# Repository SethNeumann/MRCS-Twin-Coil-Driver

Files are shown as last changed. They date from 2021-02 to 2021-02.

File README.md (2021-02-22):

# REPO NAME: MRCS-Twin-Coil-Driver
## License: Creative Commons Attribution-NonCommercial-ShareAlike

Twin Coil Machines present some challenges:

    They tend to slam the points into the stock rails, eventually damaging the connection to the throwbar and the spikes or solder holding the stock rails down 
    can loosen or break.  They make a lot of electrical noise when the power is removed from the coils, which gets into other electronics, causing false operation.
    The coils will overheat and become damaged, if not catch fire, if current is applied for an extended period.
    
    In the past, Capacitive Discharge (CD) supplies were used to make an affordable supply that would protect the coil by not recharging while connected and limiting
    the constant current in case the controls failed and permanently energized the coil.

Our design drives both mild (Atlas, Bachmann, Lifelike, Peco) and "Nasty" PFM, Tenshodo, Ken Kidder, NJ International Twin Coil type machines.  The Twin Coil Driver
(TCD) shapes the pulses driving the switch machines to soften both the physical and electrical blow, reducing electrical noise and physical impact.  Pulse timing is
done in hardware (no chance of a software hang leaving power on).  The TCD works with CD power supplies and modern power supplies such as those used for LEDs, or
inexpensive bench supplies.  

The Twin Coil Driver has internal spike suppression diodes.  Input is logic level and the coils are fired on the rising and falling edge, so a simple toggle switch 
or logic level input controls the machine.

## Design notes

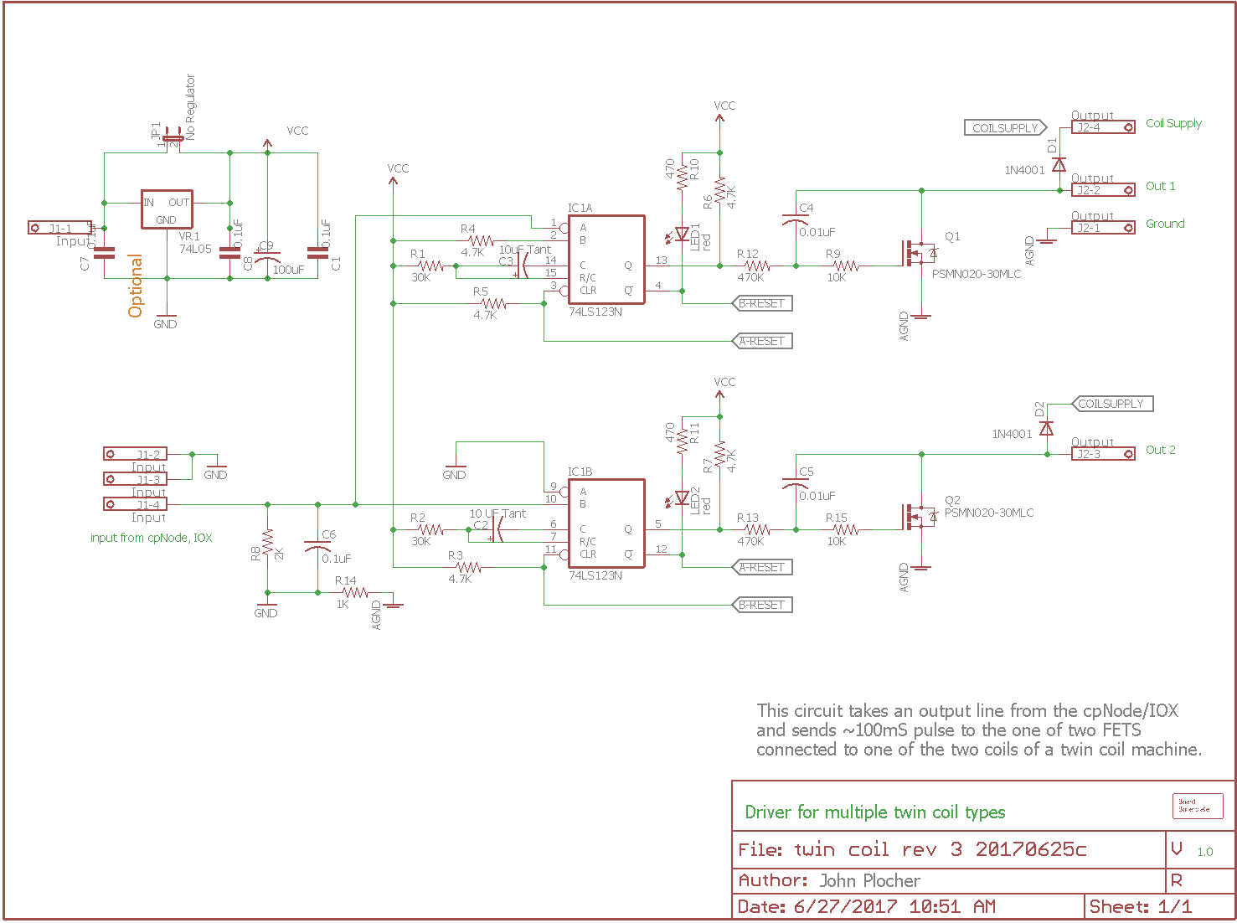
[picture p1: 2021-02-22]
MRCS-Twin-Coil-Driver-Schematic.png

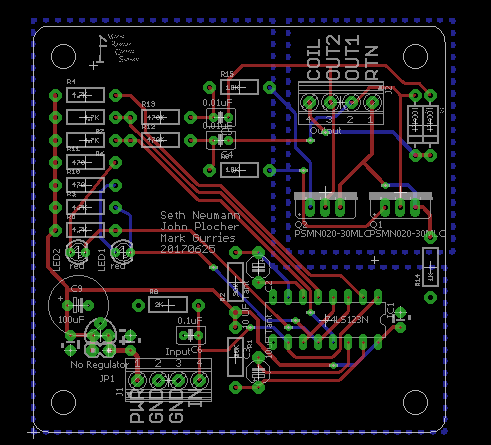
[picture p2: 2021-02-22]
MRCS-Twin-Coil-Driver-layout.png

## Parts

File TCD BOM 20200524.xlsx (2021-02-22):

Qty | Value | Device | Package | Parts | Description | MRCS | Jameco | Banggood | Leads | Leads Extd | unit | Extd | EOQ
1 |  | BOARD69X70 | BOARD-DINRAIL-2.7INX7CM | BOARD1 |  | TOB-BB |  |  |  | 0 | $1.00 | $1.00 | 5
2 | .022 uF | C-US025-030X050 | C025-030X050 | C4, C5 | CAPACITOR Monolithic .022 @ 50V 223 |  | 2306383 |  | 2 | 4 | $0.15 | $0.30 | 100
4 | 0.1uF | C-US025-030X050 | C025-030X050 | C1, C6, C7, C8 | Capacitor - Monolithic 0.1 (104) @ 50V |  | 2295911 |  | 2 | 8 | $0.02 | $0.08
2 | 10 UF Tant | CPOL-USE5-4 | E5-4 | C2, C3 | POLARIZED CAPACITOR, American symbol |  |  |  | 2 | 4 | $0.45 | $0.90 | 20
1 | 100uF | CPOL-USE3.5-10 | E3,5-10 | C9 | POLARIZED CAPACITOR, American symbol |  | 29962 |  | 2 | 2 | $0.16 | $0.16 | 10
1 | 1K | RESISTORPTH-1/4W | AXIAL-0.4 | R14 | Resistor 1K 1/4W |  | 690865 |  | 2 | 2 | $0.01 | $0.01 | 100
2 | 10K | RESISTORPTH-1/4W | AXIAL-0.4 | R9, R15 | Resistor 10K 1/4W |  | 691104 |  | 2 | 4 | $0.01 | $0.02 | 100
2 | 1N4001 | DIODEPTH | DIODE-1N4001 | D1, D2 | Diode 1N4004 |  | 35991 |  | 2 | 4 | $0.06 | $0.12 | 100
3 | 2K | RESISTORPTH-1/4W | AXIAL-0.4 | R8, 10,11 | Resistor 2K 1/4W |  | 690865 |  | 2 | 6 | $0.02 | $0.06 | 100
2 | 30K | RESISTORPTH-1/4W | AXIAL-0.4 | R1, R2 | Resistor 30K 1/4W |  | 691219 |  | 2 | 4 | $0.02 | $0.04 | 100
5 | 4.7K | RESISTORPTH-1/4W | AXIAL-0.4 | R3, R4, R5, R6, R7 | Resistor 4.7K 1/4 W |  | 691024 |  | 2 | 10 | $0.02 | $0.10 | 100
2 | 470K | RESISTORPTH-1/4W | AXIAL-0.4 | R12, R13 | Resistor, 470K 1/4W |  | 691500 |  | 2 | 4 | $0.01 | $0.02 | 100
1 | 78L05 | V_REG_78L05 | TO-92 | VR1 | Voltage Regulator |  | 51182 |  | 3 | 3 | $0.25 | $0.25 | 100
1 | 74LS123N | 74LS123N | DIL16 | IC1 | Retriggerable monostable MULTIVIBRATOR |  | 46480 |  |  | 0 | $0.79 | $0.79 | 10
2 | Input, output | 4 pos 3.5mm screw | 4 pos 3.5mm screw | J1, J2 | MKDS 1/ 4-3,5 Printklemme |  | 2124411 |  | 4 | 8 | $0.49 | $0.98 | 100
1 | socket | 16 pin DIP | 16 pin DIP | IC1-s | 16 pin DIP socket |  | 112222 |  | 16 | 16 | $0.13 | $0.13 | 100
1 | No Regulator | JUMPER-2PTH_LOCK | 1X02_LOCK | JP1 | Jumper |  |  | X | 2 | 2 | $0.02 | $0.02 | 4000
2 | PSMN020-30MLC | STP5NA50 | TO220BV | Q1, Q2 | N-CHANNEL MOS FET |  | 787798 | X | 3 | 6 | $0.59 | $1.18 | 100
1 | red | LED3MM | LED3MM | LED1 | LED Green |  |  | X | 2 | 2 | $0.01 | $0.01 | 300
1 | green | LED3MM | LED3MM | LED2 | LED Red |  |  | X | 2 | 2 | $0.01 | $0.01 | 300
 | BOM Cost |  |  |  |  |  |  |  |  | 91 |  | $6.18
 | BOM Markup | 20% |  |  |  |  |  |  |  |  |  | $1.24
 | BOM Subtotal |  |  |  |  |  |  |  |  |  |  | $7.42
 | Labor @ | $0.20 | per lead |  |  |  |  |  |  |  |  | $18.20
 | Labor Markup | 20% |  |  |  |  |  |  |  |  |  | $3.64
 | Labor Subtotal |  |  |  |  |  |  |  |  |  |  | $21.84
 | Cost Total |  |  |  |  |  |  |  |  |  |  | $29.26
 | e-Commerce | 10% |  |  |  |  |  |  |  |  |  | $2.93
 | Grand Total |  |  |  |  |  |  |  |  |  |  | $32.18
 | Sell |  |  |  |  |  |  |  |  |  |  | $32.00

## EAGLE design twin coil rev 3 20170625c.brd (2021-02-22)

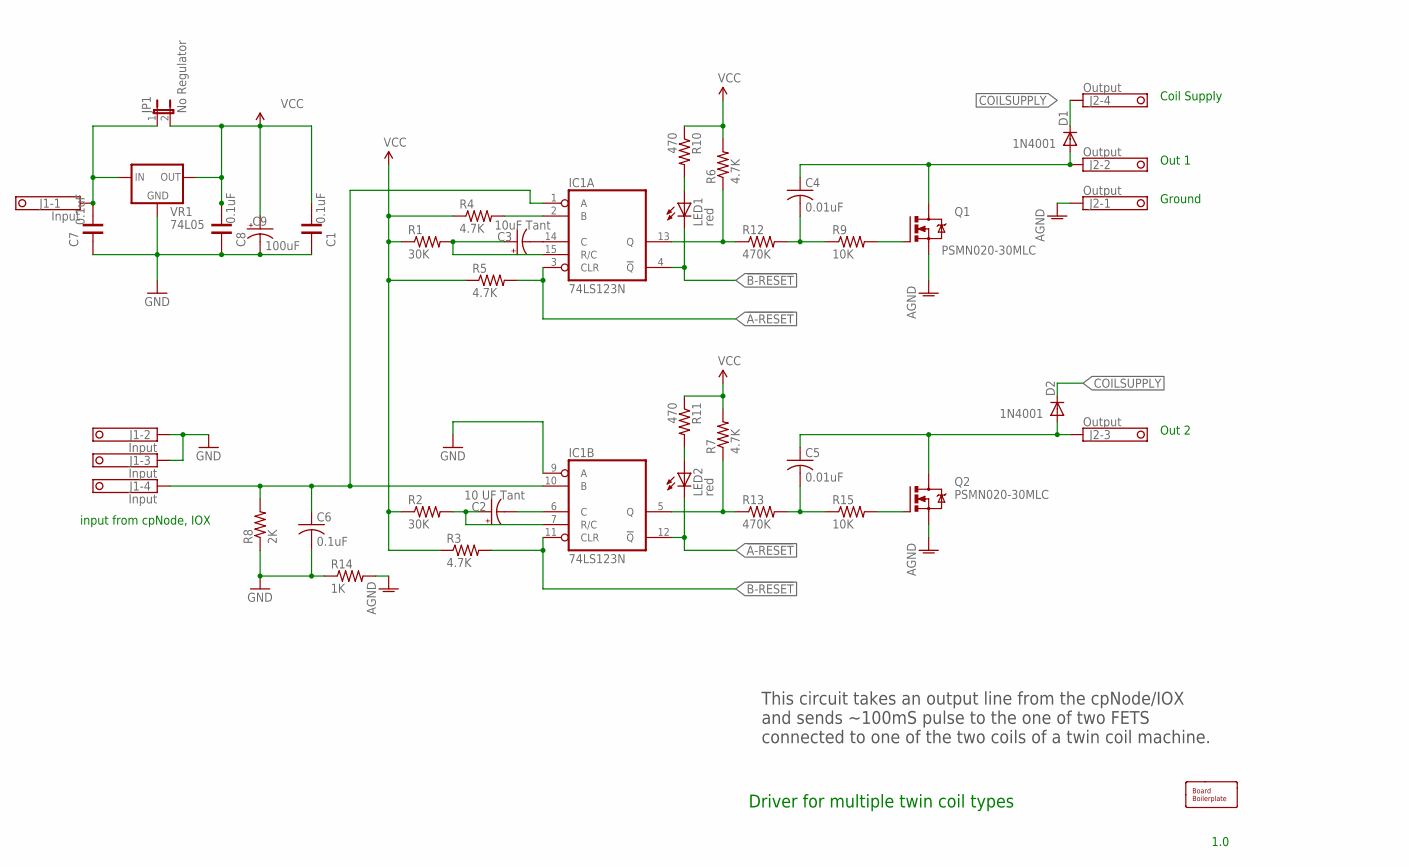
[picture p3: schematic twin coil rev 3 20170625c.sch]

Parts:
BOARD1: BOARD69X70; BOARD-DINRAIL-2.7INX7CM
C1, C7, C8: 0.1uF; CAP-PTH-SMALL
C2: 10 UF Tant; E5-4
C3: 10uF Tant; E5-4
C4, C5: 0.01uF; C025-030X050
C6: 0.1uF; C025-030X050
C9: 100uF; E3,5-10
D1, D2: 1N4001; DIODE-1N4001
IC1: 74LS123N; DIL16
J1: Input; 1751264
J2: Output; 1751264
JP1: No Regulator; 1X02_LOCK
LED1, LED2: red; LED3MM
Q1, Q2: PSMN020-30MLC; TO220BV
R1, R2: 30K; AXIAL-0.4
R3, R4, R5, R6, R7: 4.7K; AXIAL-0.4
R8: 2K; AXIAL-0.4
R9, R15: 10K; AXIAL-0.4
R10, R11: 470; AXIAL-0.4
R12, R13: 470K; AXIAL-0.4
R14: 1K; AXIAL-0.4
VR1: 74L05; TO-92

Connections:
!A-RESET: IC1.3 (CLR), IC1.12 (!Q), LED2.K (C), R5.P$2 (2)
!B-RESET: IC1.4 (!Q), IC1.11 (CLR), LED1.K (C), R3.P$2 (2)
AGND: J2.1, Q1.S, Q2.S, R14.P$2 (2)
COILSUPPLY: D1.C, D2.C, J2.4
FETDRIVE1: Q1.G, R9.P$2 (2)
GND: C1.1, C6.2, C7.1, C8.1, C9.-, IC1.8 (GND), IC1.9 (A), J1.2, J1.3, R8.P$1 (1), R14.P$1 (1), VR1.2 (GND)
INPUT: C6.1, IC1.1 (A), IC1.10 (B), J1.4, R8.P$2 (2)
unnamed: IC1.13 (Q), R6.P$1 (1), R12.P$1 (1)
unnamed: IC1.5 (Q), R7.P$1 (1), R13.P$1 (1)
unnamed: Q2.G, R15.P$2 (2)
unnamed: IC1.2 (B), R4.P$2 (2)
unnamed: C3.-, IC1.14 (C)
unnamed: C2.-, IC1.6 (C)
unnamed: C3.+, IC1.15 (R/C), R1.P$2 (2)
unnamed: C2.+, IC1.7 (R/C), R2.P$2 (2)
unnamed: C4.2, R9.P$1 (1), R12.P$2 (2)
unnamed: C5.2, R13.P$2 (2), R15.P$1 (1)
unnamed: LED1.A, R10.P$2 (2)
unnamed: LED2.A, R11.P$2 (2)
OUT1: C4.1, D1.A, J2.2, Q1.D
OUT2: C5.1, D2.A, J2.3, Q2.D
V+: C7.2, J1.1, JP1.1, VR1.3 (IN)
VCC: C1.2, C8.2, C9.+, IC1.16 (VCC), JP1.2, R1.P$1 (1), R2.P$1 (1), R3.P$1 (1), R4.P$1 (1), R5.P$1 (1), R6.P$2 (2), R7.P$2 (2), R10.P$1 (1), R11.P$1 (1), VR1.1 (OUT)

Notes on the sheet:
input from cpNode, IOX
This circuit takes an output line from the cpNode/IOX and sends ~100mS pulse to the one of two FETS connected to one of the two coils of a twin coil machine.
Coil Supply
Out 2
Out 1
Ground
Driver for multiple twin coil types
1.0

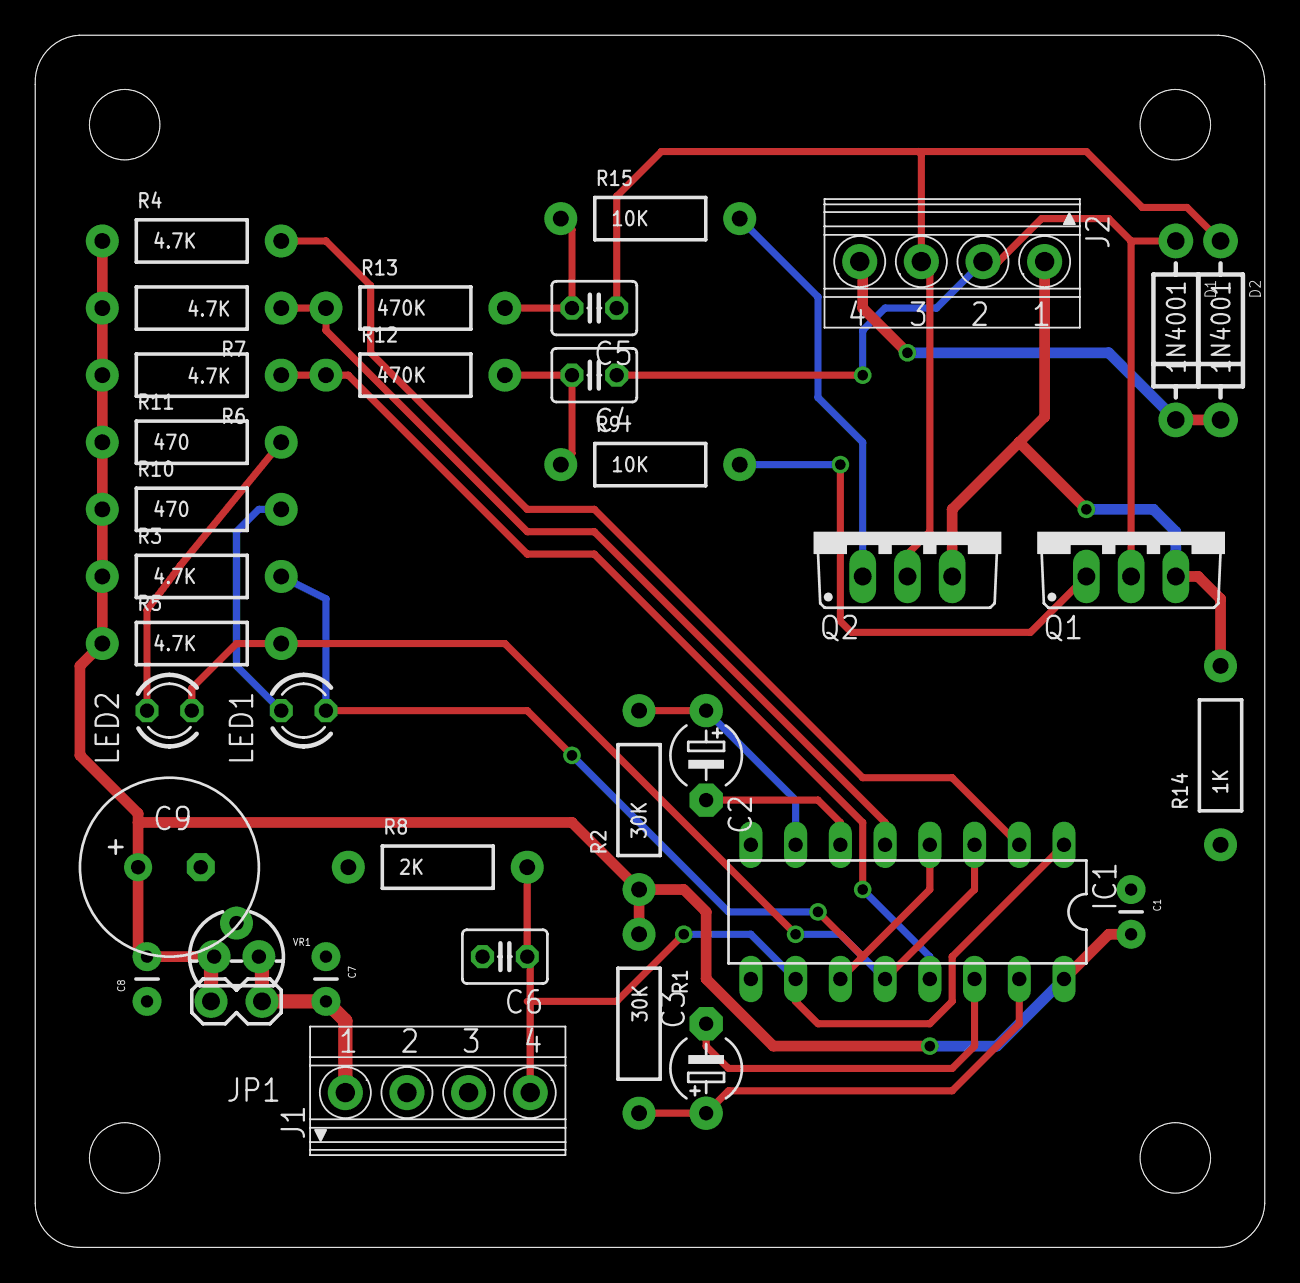
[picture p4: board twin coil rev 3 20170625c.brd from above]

Board: 2 copper layers, 69.8 x 68.8 mm, 38 parts (0 on the bottom side), 23 nets.

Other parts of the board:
U$1: CA-PROP65WARNING
U$2: MRCSLOGOTOP

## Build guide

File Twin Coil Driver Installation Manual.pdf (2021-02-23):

# Twin Coil Driver

### Revision 1.0 February 22, 2021

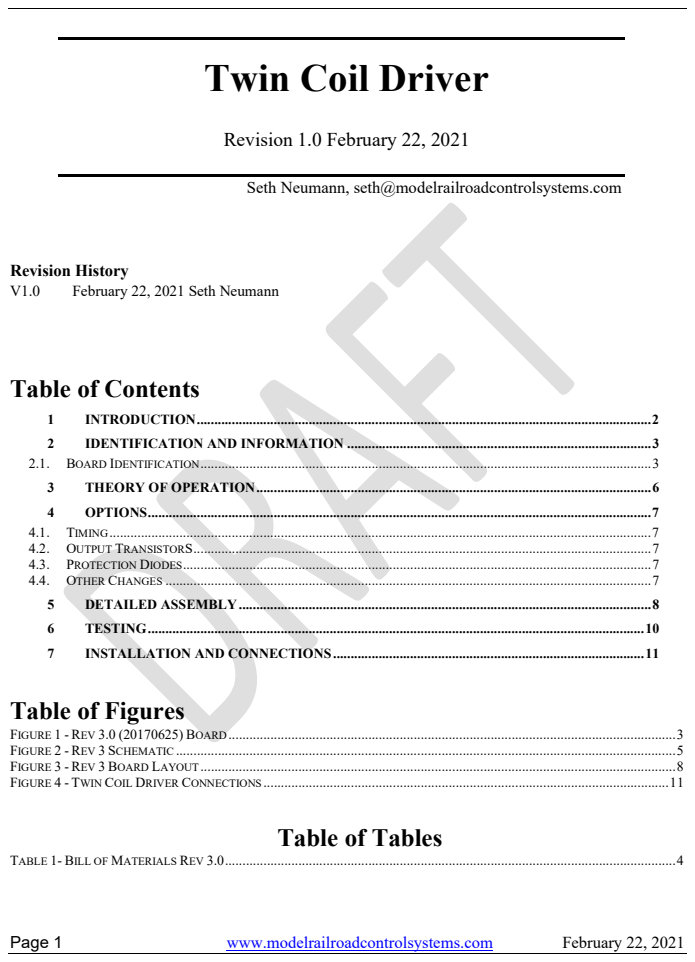
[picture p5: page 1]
Page 1; www.modelrailroadcontrolsystems.com; February 22, 2021; Revision History; February 22, 2021 Seth Neumann

Seth Neumann, seth@modelrailroadcontrolsystems.com

Table of Contents

1 INTRODUCTION .................................................................................................................................. 2
2 IDENTIFICATION AND INFORMATION ....................................................................................... 3
2.1. BOARD IDENTIFICATION ................................................................................................................................. 3
3 THEORY OF OPERATION ................................................................................................................. 6
4 OPTIONS ................................................................................................................................................ 7
4.1. TIMING ........................................................................................................................................................... 7
4.2. OUTPUT TRANSISTORS ................................................................................................................................... 7
4.3. PROTECTION DIODES ...................................................................................................................................... 7
4.4. OTHER CHANGES ........................................................................................................................................... 7
5 DETAILED ASSEMBLY ...................................................................................................................... 8
6 TESTING .............................................................................................................................................. 10
7 INSTALLATION AND CONNECTIONS ......................................................................................... 11
Table of Figures

FIGURE 1 - REV 3.0 (20170625) BOARD ................................................................................................................................ 3
FIGURE 2 - REV 3 SCHEMATIC ............................................................................................................................................... 5
FIGURE 3 - REV 3 BOARD LAYOUT ........................................................................................................................................ 8
FIGURE 4 - TWIN COIL DRIVER CONNECTIONS .................................................................................................................... 11

Table of Tables

TABLE 1- BILL OF MATERIALS REV 3.0 ................................................................................................................................. 4

Page 2 | www.modelrailroadcontrolsystems.com | February 22, 2021

### 1 INTRODUCTION

Introduction

This document describes the Twin Coil Driver and how to assemble and install it.

A lot of people have told us that the last thing MRCS (think Arduino and similar "high tech" components) would be doing is working with ancient Twin Coil switch machines. However, we do a lot of custom work, including towers and staging controllers, and some of our clients have existing twin coil machines in place, and one (an old friend in the Coast Division) has a huge hoard of them under his layout, so we designed this interface to support those applications. Twin Coil Machines present some challenges:

- They tend to slam the points into the stock rails, eventually damaging the soldered connection to the throw bar, rip the points off PC Board throw bars, and break or loosen the spikes or solder holding the stock rails down.
- They make a lot of electrical noise when power is removed from the coils, which gets into nearby electronics, sometimes causing false operation.
- The coils can overheat and become damaged, if not catch fire, if current is applied for an extended period.
- In the past, Capacitive Discharge (CD) supplies were used to make an affordable supply that would protect the coil by not recharging while connected and limiting the constant current in case the controls failed and permanently connected the coil.

Our design drives both “mild” (Atlas, Bachmann, Lifelike, Peco) and "nasty" (PFM, Tenshodo, Ken Kidder, NJ International) Twin Coil type machines. The Twin Coil Driver (TCD) shapes the pulses driving the switch machines to soften both the physical and electrical blow, reducing physical impact and electrical noise. Pulse timing is done in hardware (so there’s no chance of a software hang leaving power on). The TCD works with CD power supplies as well as modern power supplies such as those used for LEDs, or inexpensive bench supplies.

The Twin Coil Driver has internal spike suppression (“snubber”) diodes. Input is logic level and the coils are fired on the rising and falling edge, so a simple toggle switch or logic level input can control the interface.

This circuit board has:

- An on-board regulator to drop 12V layout auxiliary bus power to 5 logic (you can omit the is building your own, but it does provide additional protection against noise).
- On-board LEDs for indicating when the board sending pulses to each coil.“Snubber” diodes to protect against reverse voltage surges when
- The Twin Coil Driver operates from 12V and draws about 3 mA idle.
- The Twin Coil Driver uses standard semiconductors available from Jameco, Digikey and similar suppliers.
- Provides a 1 second pulse to operate the coils
- Open drain active low outputs momentarily sinks up to 2A at 40V

All components are through-hole technology for ease of assembly and repair.

External connection pads are on 3.5mm centers.

### 2 IDENTIFICATION AND INFORMATION

### 2.1. BOARD IDENTIFICATION

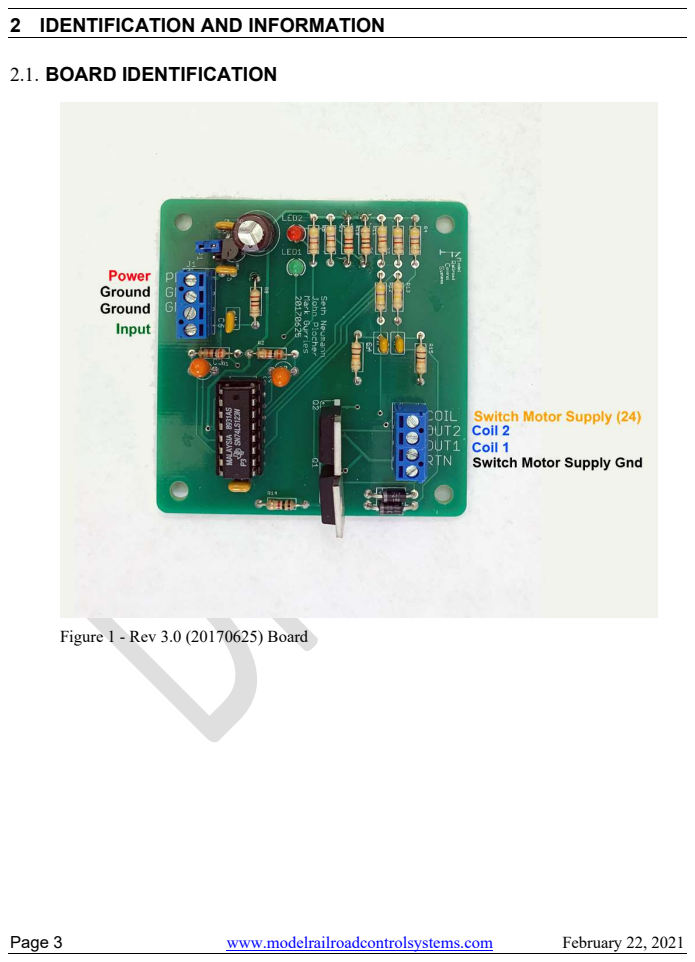
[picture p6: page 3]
Page 3; www.modelrailroadcontrolsystems.com; February 22, 2021

Figure 1 - Rev 3.0 (20170625) Board

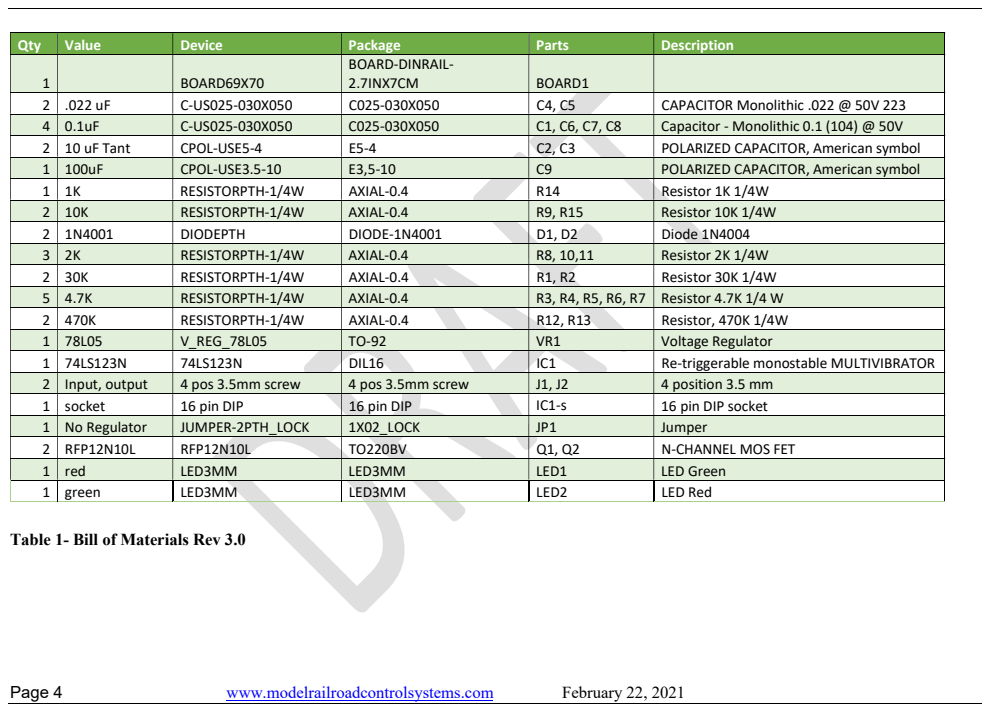
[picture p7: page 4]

Qty | Value | Device | Package | Parts | Description
1 BOARD69X70 | | | BOARD-DINRAIL-2.7INX7CM | BOARD1

2 | .022 uF | C-US025-030X050 | C025-030X050 | C4, C5 | CAPACITOR Monolithic .022 @ 50V 223
4 | 0.1uF | C-US025-030X050 | C025-030X050 | C1, C6, C7, C8 | Capacitor - Monolithic 0.1 (104) @ 50V
2 | 10 uF Tant | CPOL-USE5-4 | E5-4 | C2, C3 | POLARIZED CAPACITOR, American symbol
1 | 100uF | CPOL-USE3.5-10 | E3,5-10 | C9 | POLARIZED CAPACITOR, American symbol
1 | 1K | RESISTORPTH-1/4W | AXIAL-0.4 | R14 | Resistor 1K 1/4W
2 | 10K | RESISTORPTH-1/4W | AXIAL-0.4 | R9, R15 | Resistor 10K 1/4W
2 | 1N4001 | DIODEPTH | DIODE-1N4001 | D1, D2 | Diode 1N4004
3 | 2K | RESISTORPTH-1/4W | AXIAL-0.4 | R8, 10,11 | Resistor 2K 1/4W
2 | 30K | RESISTORPTH-1/4W | AXIAL-0.4 | R1, R2 | Resistor 30K 1/4W
5 | 4.7K | RESISTORPTH-1/4W | AXIAL-0.4 | R3, R4, R5, R6, R7 | Resistor 4.7K 1/4 W
2 | 470K | RESISTORPTH-1/4W | AXIAL-0.4 | R12, R13 | Resistor, 470K 1/4W
1 | 78L05 | V_REG_78L05 | TO-92 | VR1 | Voltage Regulator
1 | 74LS123N | 74LS123N | DIL16 | IC1 | Re-triggerable monostable MULTIVIBRATOR
2 | Input, output | 4 pos 3.5mm screw | 4 pos 3.5mm screw | J1, J2 | 4 position 3.5 mm
1 | socket | 16 pin DIP | 16 pin DIP | IC1-s | 16 pin DIP socket
1 | No Regulator | JUMPER-2PTH_LOCK | 1X02_LOCK | JP1 | Jumper
2 | RFP12N10L | RFP12N10L | TO220BV | Q1, Q2 | N-CHANNEL MOS FET
1 | red | LED3MM | LED3MM | LED1 | LED Green
1 | green | LED3MM | LED3MM | LED2 | LED Red

Table 1- Bill of Materials Rev 3.0

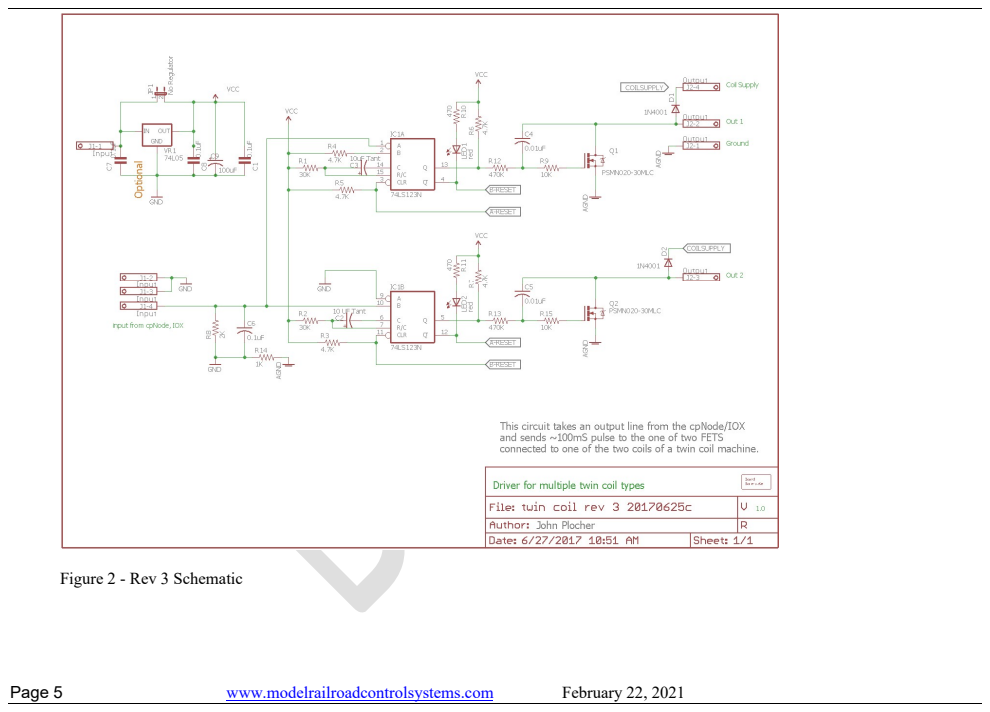
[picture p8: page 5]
Page 5; www.modelrailroadcontrolsystems.com; February 22, 2021

Figure 2 - Rev 3 Schematic

Page 6 | www.modelrailroadcontrolsystems.com | February 22, 2021

### 3 THEORY OF OPERATION

The Twin Coil Driver uses the venerable 74LS123 Dual Re-Triggerable Monostable Multivibrator https://www.google.com/url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 (search on 74LS1223 data sheet) to develop a timed pulse on two outputs (one for each of the “twin” coils. Pulse width is set by R1/C3 for the rising edge and R2/C2 for the falling edge. You can adjust these values within wide limits (see also Designing with the 74LS123 https://www.google.com/url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 )

(Search on “Designing with the 74LS123”)

The respective outputs (Pin 13 for the upward edge and Pin 3 for the downward edge) are coupled to high power FETs and drive the indicator LEDs. Other than the timing capacitors being tantalum, there is no magic to any of these components. Any handy N-channel MOS FET in a TO-220 package should do. If you are using a “mild” switch machine (most newer machines designed for N scale turnouts) you can probably get away with a smaller FET but check that the maximum drain current and voltage are compatible with your motor and power supply.

The output pulse will operate the twin coil machine and shut off before it can overheat. The board can be used in many “One Shot” applications: in one case we used it to operate relay to deliver a 3 second burst of ringing voltage to a telephone bell, this might also be used for an approach bell in an interlocking plant.

Page 7 | www.modelrailroadcontrolsystems.com | February 22, 2021

### 4 OPTIONS

### 4.1.TIMING

Pulse length is set by R1/C3 for the rising edge and R2/C2 for the falling edge. You can adjust these values within wide limits

(see also “Designing with the 74LS123” by Texas Instruments. https://www.google.com/url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

)

### 4.2.OUTPUT TRANSISTORS

I used Jameco part 787798, Fairchild RFP12N10L but any comparable N-Channel power MOSFET in a TO220 package will do. This is a “whatever is handy on the workbench” part.

### 4.3.PROTECTION DIODES

D1 and D2 are provided as snubbers to short out reverse spikes caused by collapsing magnetic fields on the solenoid coils. They are not required (but won’t hurt) if there are existing snubbers in place across the coils.

### 4.4.OTHER CHANGES

This is a fairly low-volume board and is usually built to order. If you’d like a different layout, different connectors or a custom build, please contact us at sales@modelrailroadcontrolsystems.com. You can also follow the links on the product page to my Github page and download the EAGLE CAD files and make your own modifications subject to the Creative Commons License. We’d love to see what you come with!

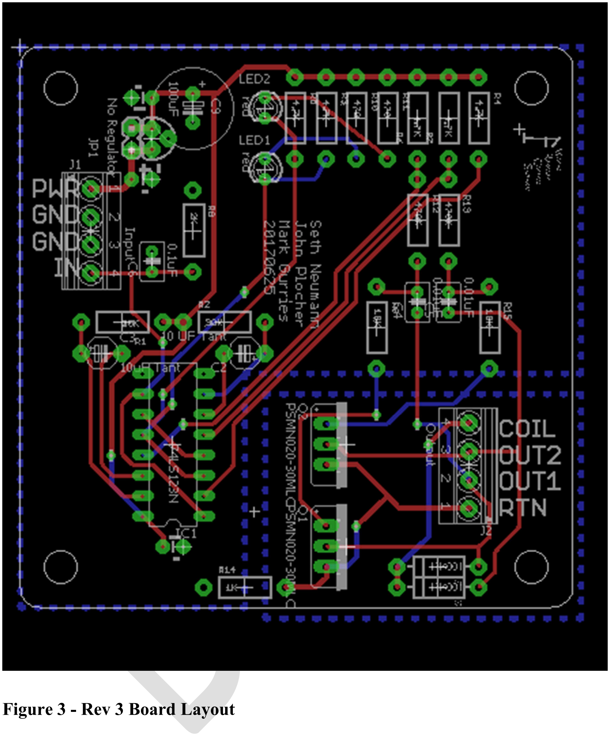
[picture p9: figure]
Figure 3 - Rev 3 Board Layout

Page 8 | www.modelrailroadcontrolsystems.com | February 22, 2021

### 5 DETAILED ASSEMBLY

All of the components are through-hole technology with wire leads. A lead bender is a useful tool is for forming the leads at 90 degrees for easy insertion into the pad holes. The general rule is installing the lowest components first, working towards components that are higher off the board. Start by inserting the lower height components (resistors and diodes). This helps you support the low components as you solder them from the bottom of the board. A small piece of cardboard may be placed over the component side as you flip it over to solder. I use thin (.015) solder to help control the amount of solder on the work.

Page 9 | www.modelrailroadcontrolsystems.com | February 22, 2021

[ ] Resistors, Diodes
[ ] Install Resistors R1 through R15. Try to keep the gold tolerance band on the right side or bottom for easier reading of values. Note that some values on the board are different from the BOM, I suggest using the BOM values.
[ ] Install diodes D1,D2 observe polarity. (You may omit these if the load already has snubbing diodes Installed – see options above)

[ ] IC Socket U1
[ ] install U1, notch pointing down in the layout above.

[ ] LEDs LED1, LED2
Install the LEDs observing polarity, they don’t have to be different colors but I find it easier to see which is which when troubleshooting in the field when the colors are different.

[ ] Monolithic Capacitors
[ ] Install the .022 uF caps C4, C5
[ ] Install the .01 uF caps C1, C6, C7, C8

[ ] Voltage Regulator VR1
[ ] Install the 78L05 regulator – note if you will be powering from a local 5V source, you can omit the regulator and use a jumper on JP1 or just wire across the terminals of JP1. See options above.

[ ] Screw Terminals J1,J2
Install 3.5mm screw terminals J1, J2

[ ] Input Jumper JP1
Install JP1 - Used if no VR1 or if you want handy tie points for input power and +5

[ ] Tantalum Capacitors C2, C3
[ ] Install C2,C3, observe polarity

[ ] Electrolytic Capacitor C9
[ ] Install Electrolytic capacitor C9 100 uF @ 50V, observe polarity

[ ] Output Transistors Q1, Q2
[ ] Install Power N channel MOSFETs with the exposed metal fins to the bars on the silk screen.

[ ] Integrated Circuit U1
You may want to power up and check that there is 5V on pin 16 (lower left) before
[ ] insert the 74LS123.

[ ] Clean the board
I clean excess flux and bits of solder off with 91% isopropyl alcohol and an old toothbrush. If you have an ultrasonic cleaner, use it, in A WELL-VENTILATED AREA, do not breath fumes or put your hands in the bath with the cleaner on. If there is still a residual layer of scuzz, use the ultrasonic with distilled or RO water and soap and rinse. I’ve also had good luck with the top rack of the dishwasher.

Page 10 | www.modelrailroadcontrolsystems.com | February 22, 2021

### 6 TESTING

Testing your Twin Coil Driver:

### 1. Mount the board securely on standoffs or in a piece of our 7CM DINRail (Tyco Track)

2. Apply positive voltage (7.5-15 VDC) between PWR (+) and one of the GND terminals on J1 on the upper left of the board. Check that 5V is appearing on pin 16 of U1.

### 3. Remove power while completing Twin Coil Motor connections

4. Connect your motor’s common lead (or one side of each coil) to your power supply + and run a jumper (22 Ga or larger) to the “Coil” terminal on J2 of the TCD.
5. Connect the other ends of the coils to Out 1 and Out 2 of J2 respectively.
6. Run a jumper from the supply ground to the RTN (return) terminal on J2.
7. Make a test jumper with a 4.7K resistor (or 10K it isn’t critical) to the 5V terminal (top) on JP1and touch the “IN” terminal on J1. The twin coil should operate, and the green LED should flash. Remove the jumper from IN and the other coil should operate, and the red LED should flash.

Page 11 | www.modelrailroadcontrolsystems.com | February 22, 2021

### 7 INSTALLATION AND CONNECTIONS

Twin Coil Machine

Input
cpOD, IOX,
SMINI, etc. | Out 1 | Twin Coil
Supply Out 2

### 12 V

Layout
power

Figure 4 - Twin Coil Driver Connections

The Installation process is like the test procedure described above:

### 1. Mount the board securely on standoffs or in a piece of our 7CM DINRail (Tyco Track)

2. Apply positive voltage (7.5-15 VDC) between PWR (+) and one of the GND terminals on J1 on the upper left of the board. Use at least 22 Ga wire.
3. Connect your motor’s common lead (or one side of each coil) to your power supply + and run a jumper (22 Ga or larger) to the “Coil” terminal on J2 of the TCD.
4. Connect the other ends of the coils to Out 1 and Out 2 of J2 respectively.
5. Run a jumper from the supply ground to the RTN (return) terminal on J2.
6. Wire the input to either a pushbutton (pull up to 5V through a 4.7K – 10K resistor) or to an Arduino such as a cpNode, IOX or other logic level output. If using an open collector output like an SMINI or DOUT, you may need a pull up as used for a push button.

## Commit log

2021-02-22 intial commit
    from the old EAGLE Directory
    [TCD BOM 20200524.xlsx, twin coil rev 3 20170625c.brd, twin coil rev 3 20170625c.sch]
2021-02-22 deleted template files
    deleted files from template, using working files from EAGLE
    [EagleTemplate-new.brd, EagleTemplate-new.sch]

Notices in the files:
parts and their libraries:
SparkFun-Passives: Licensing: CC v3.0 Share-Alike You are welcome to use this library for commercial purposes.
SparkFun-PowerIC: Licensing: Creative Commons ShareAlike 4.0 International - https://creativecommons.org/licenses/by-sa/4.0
